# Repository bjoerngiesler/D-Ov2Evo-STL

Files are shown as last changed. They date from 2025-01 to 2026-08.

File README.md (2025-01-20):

# D-Ov2Evo
Bavarian Builders: Felix Beyer, Björn Giesler

## This is an ADD-ON to Michael Baddeley's files!

This GitHub contains modified print files that are to be used as add-ons and partial replacements of Michael Baddeley's D-Ov2. This GitHub does not contain all the files to print a functional droid, you still need parts from [Michael's Patreon](https://www.patreon.com/c/mrbaddeley). We have Michael's express permission to post our modifications on GitHub to better handle file changes, upgrades etc., but will never post all files for a functional droid here.

## What is D-Ov2Evo?

D-Ov2Evo is an extension of Michael Baddeley’s great D-Ov2 design for the D-O Astromech Droid from The Rise of Skywalker. 

D-Ov2 in itself is an extension and improvement of Michael’s original D-Ov1 design. Where D-Ov1 had a central drive axis for the main wheels, D-Ov2 has an excentric Lazy Susan design, which allows fixing the wheels all around the body, giving tremendously higher stability and longevity. Where D-Ov1 had the main neck and head nod servos in the body, D-Ov2 has the head nod servo in the headbox, which greatly improves play in the head assembly.

D-Ov2Evo improves D-O in the following respects.

* All analog servos have been replaced by Dynamixel digital servos, which are serially controlled. This reduces servo play, jitter, and noise. It removes 3 out of 4 servo cables routed through the neck. It also allows much tighter control and diagnostics.
* The motors have been replaced by the same model fitted with quadrature encoders, allowing for individual wheel speed control as part of a more stable control concept. They are also actively cooled so they will never overheat.
* The whole droid is controlled by a central more powerful Arduino, and uses a modern IMU, for tighter control and the opportunity to run free head animation (e.g. turning/leaning the head automatically as the droid drives a curve).
* Power is provided by two easily removable 18650 battery packs, which yield a bit less runtime than the original LiPos but can be changed in seconds without disassembly (and are safer).
* The body takes 5W speakers instead of the original 3W ones, giving much louder sound for conventions.
* A central power supply and distribution board includes a fuse, a voltage monitor, and means much less cabling.
* The head has moving antennas run from their own microcontroller.
* The software is fully open source and published at https://github.com/bjoerngiesler/BBDroids. 

## How to Build!

**Note:** This is not a beginner project. You should have a well working printer, soldering experience, and understanding and alertness to question our instructions. We are not perfect, and there may be bugs.

You will find the print files for D-Ov2Evo in this directory and its subdirectories. The directory structure mirrors the original D-Ov2 directory structure. Each folder underneath here only contains our modified files, not copies of the original print files, so please use the D-Ov2 originals for everything not in here. Each folder also contains an Instructions file, that contains the list of original and modified files for the part, printing and materials advice, and some instructions on assembly.

You will find the systems and wiring diagram, the electronics BOM, and other documentation, in the BBDroids Wiki: https://github.com/bjoerngiesler/BBDroids/wiki/91-Individual-Droid:-D%E2%80%90Ov2Evo If something is not clear, please check the Wiki first, and if you still have questions there is a discussion board at https://github.com/bjoerngiesler/BBDroids/discussions that you can use for questions. Please search before you ask, maybe someone already answered your question!

**Note:** The head with the movable aerials is optional. It is fancy, and we will add more antenna animation as things progress; but it also adds quite some weight to the head and work and cost to your list. You can also simply build the head assembly from the original D-Ov2 plans, with static antennas. Print `HeadStaticAerialsDynamixelCutout.stl` instead of the original head cone, because the roll Dynamixel sticks out at the top and this one has a cutout for it.

## Work in Progress! (But almost done)

D-Ov2Evo has been in development for more than a year. It started with taking a lot of inspiration from Matt Denton’s Dynamixel/Lynxmotion modification of the original D-Ov1.

Over time, we learned, added and modified many things. Björn’s original D-Ov2Evo ran great at a convention for a day, and on the second day one motor burned up… we need active cooling. Getting the batteries out and back in is a huge hassle… we need to modify for removable batteries. The thing is much too silent… we need bigger speakers. You can’t get at the grub screws for the motor gears. The cabling is a mess. And so on and so on. 

We are actively stopping ourselves now from doing any more modifications, it’s time the thing gets tested by other people. But as we publish, we are building two droids as test kits, and making how-to videos. As this slowly progresses, we are going to publish the files to Michael Baddeley’s OneDrive, and we are also going to publish extensive (and hopefully correct :-)) videos that guide through physical build, electronics, control system tuning, and software.

Please bear with us, we’ll arrive at the head eventually.

If you have any questions or suggestions, you can find Felix and Björn in MrBaddeley’s Facebook group, please ping us there in posts or send us PMs.

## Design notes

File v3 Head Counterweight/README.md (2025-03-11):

# Why is a head counterweight significant?

In the original D-O files developed by Michael, the head weight is not balanced by its own counterweight. This means that every head motion changes the body weight distribution, especially if the neck tilts moving the head forward or backward. This causes the body to pitch forward or backward, influencing the body balance controller that is trying its very best to keep the body in equilibrium. Essentially this means that as you bring the head forward, the body pitches forward and starts to drive forward as the controller tries to compensate for that pitch. Not only the neck servo goes into this equation, but also the head motion on the neck itself. This makes the effect hard to compensate by software unless you know the exact weight distribution of all head and neck components and also the speed they are moving at and the torque their motors are enacting on the system.

These effects are the main reason why it is a very good idea to reduce head weight to an absolute minimum, but if we want to have movable aerials in the head for example there are limits to the weight reduction. Adding a counterweight to the head itself helps tremendously to decouple head from body motion, allowing for much more freedom in head materials and actuators.

The counterweight that James designed can add around 1kg of weight to balance out the head weight. Since the head lever is much longer, that additional kg is needed even though the head itself is only about 300g.

# Will the non-counterweight version be supported?

Only with static aerials unfortunately. If you know what you are doing you can certainly get a heavier head to control, all the parameters are there and an article describing how they interact is coming. But it is not easy to remove all residual drift, and remotely supporting this is far beyond the amount of time we can invest. We therefore heavily recommend making this change, even if it needs reprints.

# What do I need to change?

Unfortunately this requires a number of reprints - but it's really worth it!

You need a new main frame and top frame to make room for the counterweight, a new main axle to attach the counterweight to, and of course the counterweight pendulum itself. There is a new servo mount and servo main gear. There is also a new PCB base for the main board (which brings additional advantages and tweaks - e.g. you can now remove the PCB base and main board without unscrewing the top frame). You can find these files here: https://github.com/.../tree/main/v3%20Head%20Counterweight. The pendulum can be printed in one part, there is also a cut version that should be glued together with CA glue.

After printing, fill the main frame with 1-1.5kg of ballast and pour with epoxy. Fill the pendulum up to the brim with ballast, you should be able to get just short of 1kg of weight in there if you use lead. Make sure all the nooks and crannies are filled by shaking and pushing from the top. Epoxy is optional here, because the main bar will hold the ballast in place. If you want you can also fill the main bar with ballast, this is optional as it doesn't contribute a lot. The counterweight does not need to be exact - as you see from the video with just head and counterweight outside the body, the balance is not perfect with mine and it doesn't need to be; we still have the body counterweight and friction in the servo to take care of the delta. But it is a good idea to at least roughly try to assemble head,

Add square nuts to all the holes in main frame, top frame and pendulum, and secure with hot glue.

Set the pendulum aside, assemble servo and servo base, insert into main frame. Make sure the servo gear is at zero before you proceed.

Add the main bar and side panels with the large bearings. Now put the pendulum underneath the main bar into the cutout in the main frame and screw it on.

Add the top frame with power board and the PCB base with main board and cable everything up.

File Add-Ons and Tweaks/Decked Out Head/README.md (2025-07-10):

# Decked Out Head

This directory contains files for what we call the "Decked Out Head". It's a one-piece head with a separate eye tray and eye covers / "lenses" that can be used to add LED "eyes" to D-O. There is also a variant that allows mounting a FPV camera in the head cone.

This head absolutely needs a neck counterweight, it is too heavy otherwise. Even so, it should be printed in LW-PLA for weight reduction. D-O will drive with a decked out head in regular PLA but you will definitely notice the extra weight. At least for the version with the camera mount, it also will not print properly without supports. This definitely makes it a challenging print. Know what you're signing up for :-)

## Parts
* Headlight tint spray (I use https://www.amazon.de/dp/B0CTCSPR32)
* 3 WS2812 LED strips with 20 LEDs each (e.g. https://de.aliexpress.com/item/4000197861280.html)
* Optional FPV camera: Wyvern Link VTX 100mW transmitter (https://de.banggood.com/Emax-Wyvern-Link-AlphaOpenIPC-100mW-Video-Transmitter-VTX-for-RC-Drone-p-2022191.html)
* Optional FPV cam receiver (https://www.banggood.com/Emax-Wyvern-Link-AlphaOpenIPC-100mW-Video-Receiver-VRX-p-2022194.html)
* On the Qt Py in the head, use the board with the Neopixel connector, not the one without. SMD solder the Neopixel connector on first, if it isn't already. Make sure that you also solder the side tabs, as they will take the mechanical strain from inserting the cable later - if you don't there is a good chance of breaking off the connector. Ask me how I know.

## Printing and Assembly Instructions
1. Print the head variant of your choice, and the eye tray. 
2. Print the eye lens three times in regular white PLA.
3. Paint the eye lenses with a couple coats of headlight tint spray until they are as dark as you would like them.
4. Cut 3 LEDs off each of the LED strips, leaving 17 LEDs on each strip. Cut off the side without the cable, and make sure that you leave enough of the soldering pads intact that you can still solder cables to them.
5. Cut the connectors off the end of the cables on 2 of the strips, and strip the ends of the cables with a wire stripper to expose a mm or so of bare wire.
6. Use double sided tape to mount the LED strips in the eye tray. The left eye gets the strip with the connector on it; push the connector through the hole at the top. The strip for the middle eye is mounted upside down; route the cable out the bottom and into the bottom hole on the left strip. The strip for the right eye is mounted with the cable pointing up; route it out the top and into the top hole on the middle strip.
7. Carefully connect the three strips by soldering the cables from the middle to the left and from the right to the middle strip, matching the colors of the cables coming out the other side. Lift the strip ends with the solder pads out of the eye tray for this so you don't heat up the eye tray's PLA.

## Connecting the Neopixel strips
This is a bit awkward for the current generation of boards. We are updating the board but at the moment you have to do some wiring and modification on the connector.

1. SMD solder the connector onto the board if it is not already on - BEFORE soldering the board to the Qt Py. 
2. Solder a wire from the board's +5V input to the pin taking ESP32's +5V input.
3. Solder a wire from the pin taking the ESP32's RX pin (it's the one farthest away from the +5V input on the same side) to the small hole on the board marked "NP" or "Neopixel".
4. Solder the board to the Qt Py using a pin header, connecting all 6 pins on the +5V side of the Qt Py, +5V pin farthest away from the Neopixel connector, USB-C port pointing down.
5. Do not plug the Neopixel strip in yet. Plug the board into USB-C and measure the connection. It should have GND on the pin next to the "NP" hole, the connection to "NP" on the middle pin, and the connection to +5V on the pin closest to the ESP32 board. Make sure that your cable reflects that mapping - black wire is GND, red wire is +5V, and white wire is Data or "NP". You can rewire the cable by carefully lifting up the plastic tabs holding the pins with a needle and gently pulling the pins out and reinserting them into the correct holes.

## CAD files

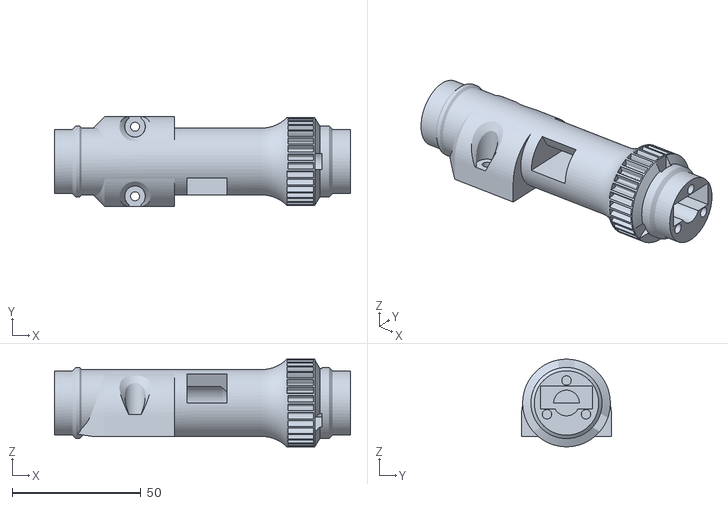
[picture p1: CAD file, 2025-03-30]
MainBar/MainBar_Counterweight_10Pin_Socket_Connector.stl
114.9 x 35.0 x 34.0

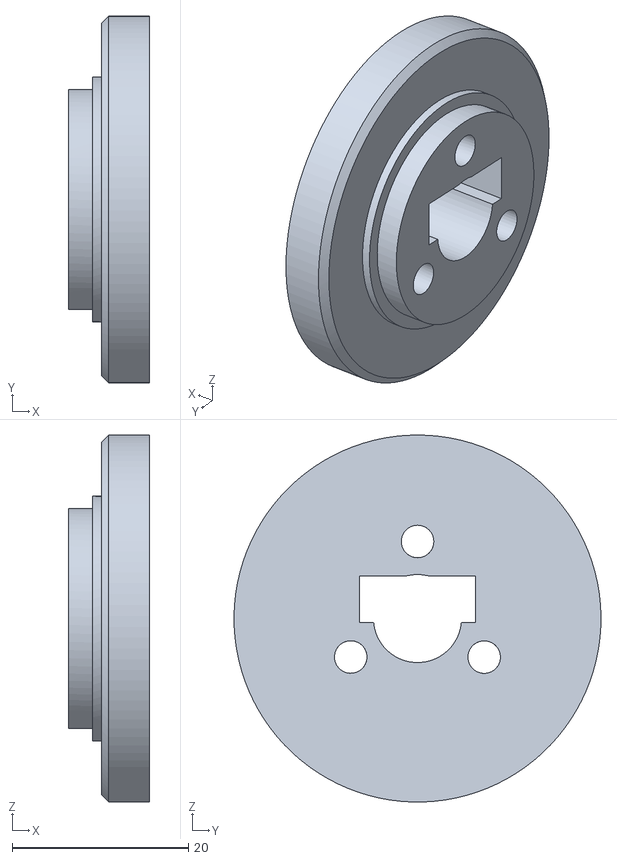
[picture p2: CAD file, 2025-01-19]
MainBar/MainBarHolderB_Connector_Cutout.stl
9.16 x 41.7 x 41.7

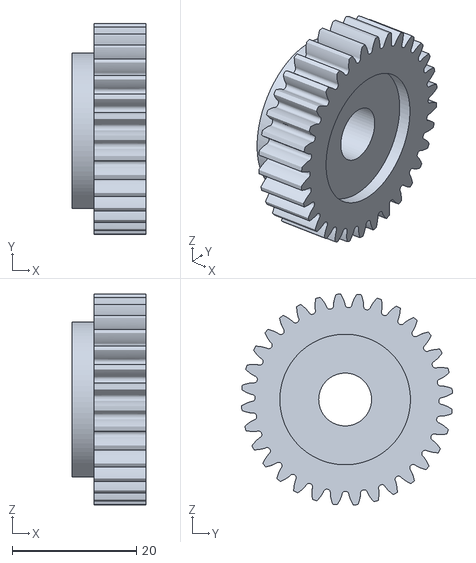
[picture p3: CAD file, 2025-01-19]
MainFrame/Main Servo Gear Dynamixel.stl
11.9 x 33.9 x 33.9

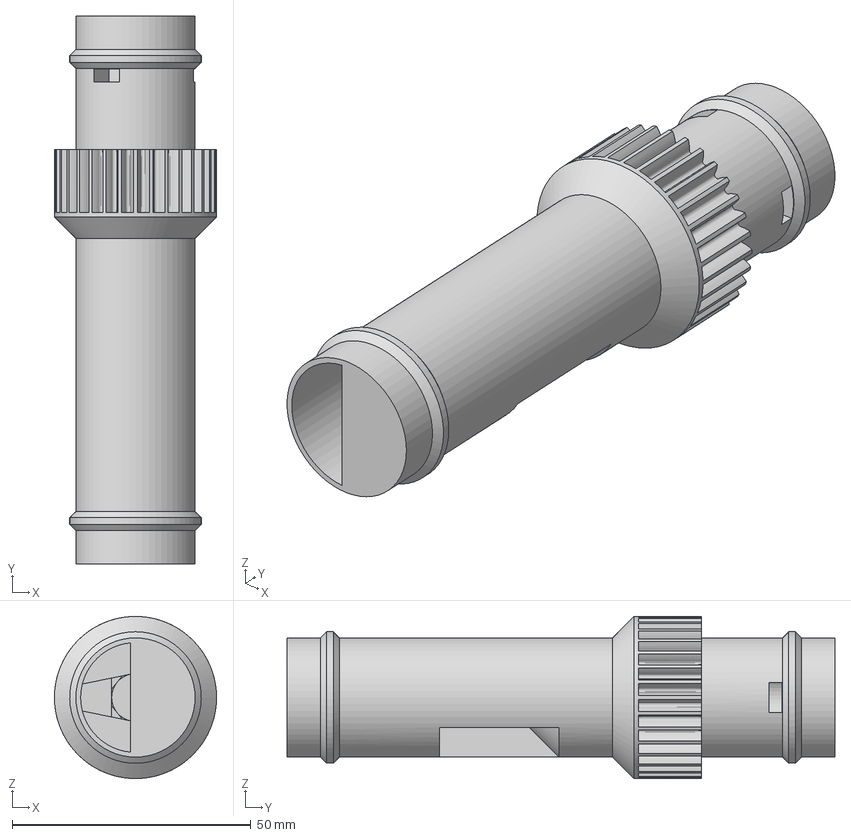
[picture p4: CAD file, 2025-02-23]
MainBar_Counterweight_10Pin_Socket_Connector_Printoptimized.3mf
34.0 x 114.9 x 34.0 mm

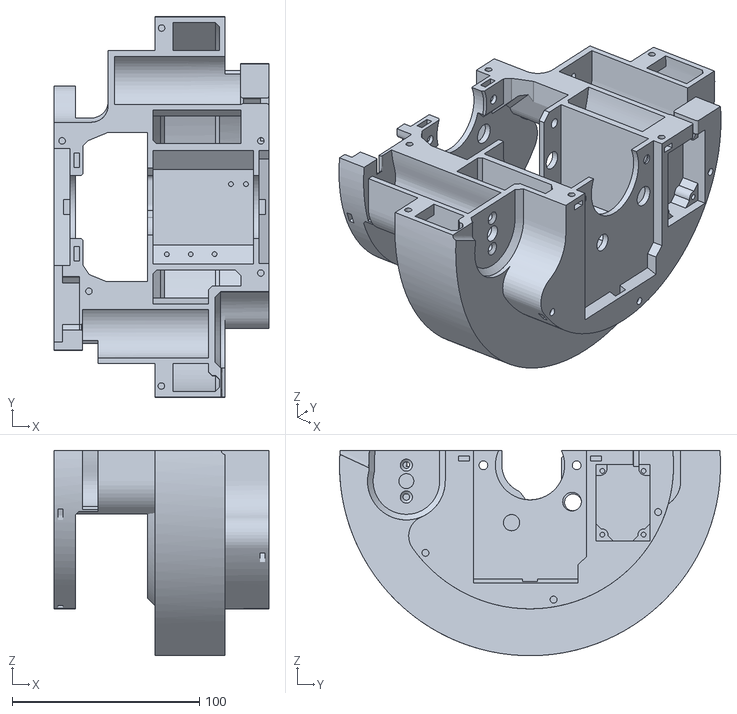
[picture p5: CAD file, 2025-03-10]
v3 Head Counterweight/Mechanics/Main Frame.stl
114.5 x 203.3 x 109.6

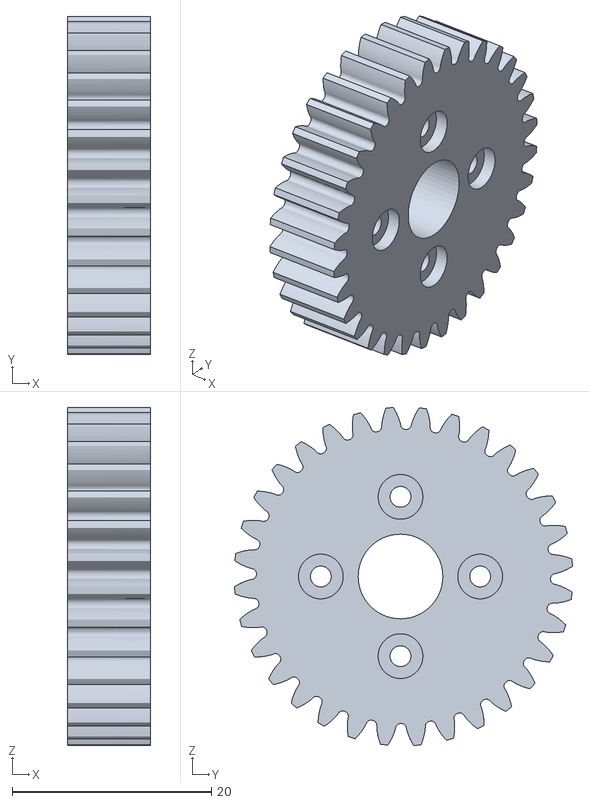
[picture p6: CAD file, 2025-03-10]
v3 Head Counterweight/Mechanics/Main Servo Gear Dynamixel.stl
8.35 x 33.9 x 33.9

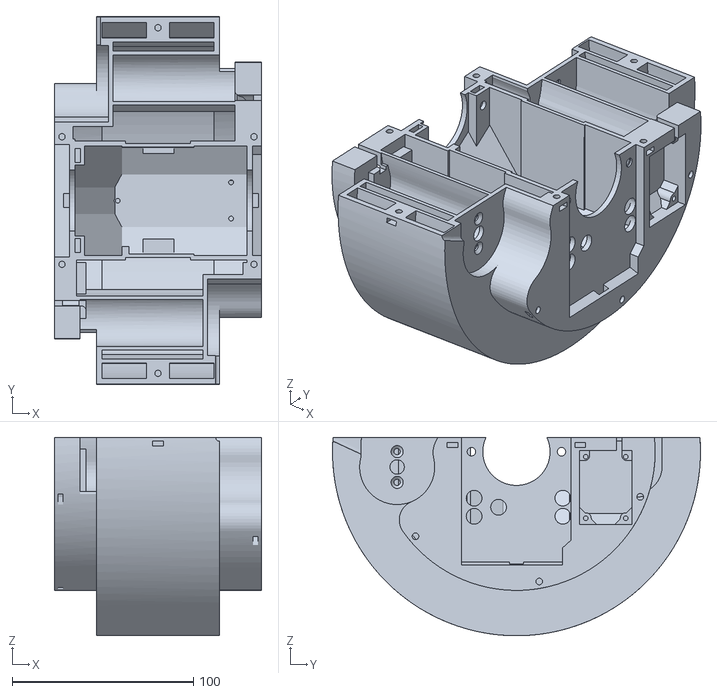
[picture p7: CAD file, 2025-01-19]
MainFrame/Main Frame Dynamixel 5WSpeakers.stl
114.5 x 203.3 x 109.6

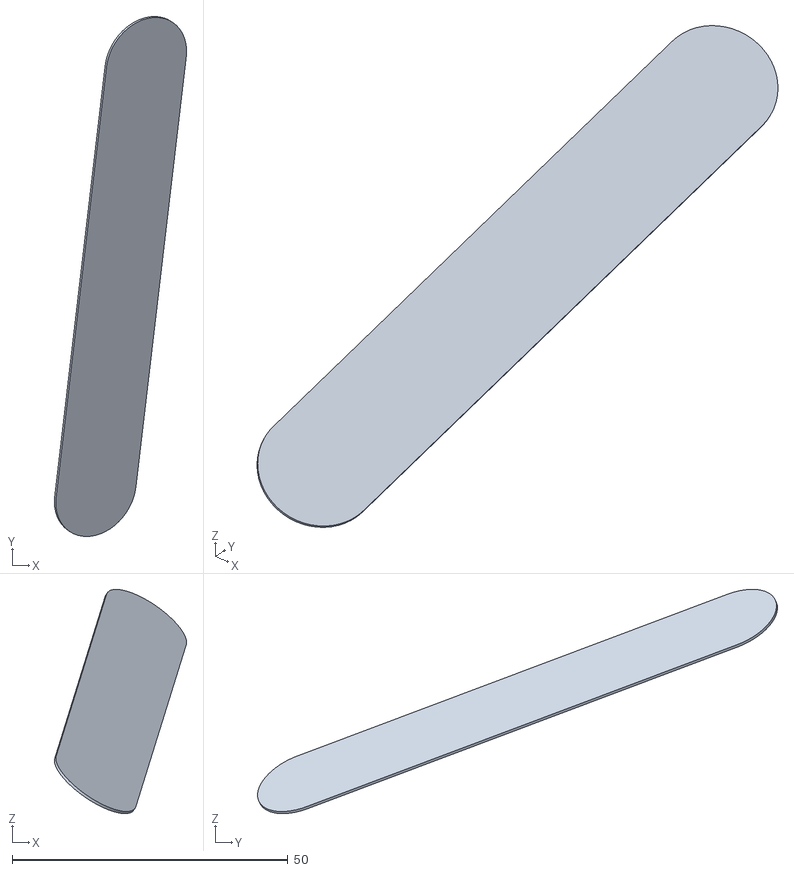
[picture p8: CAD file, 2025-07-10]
Add-Ons and Tweaks/Decked Out Head/Eye Lens x3.stl
24.0 x 94.3 x 40.7

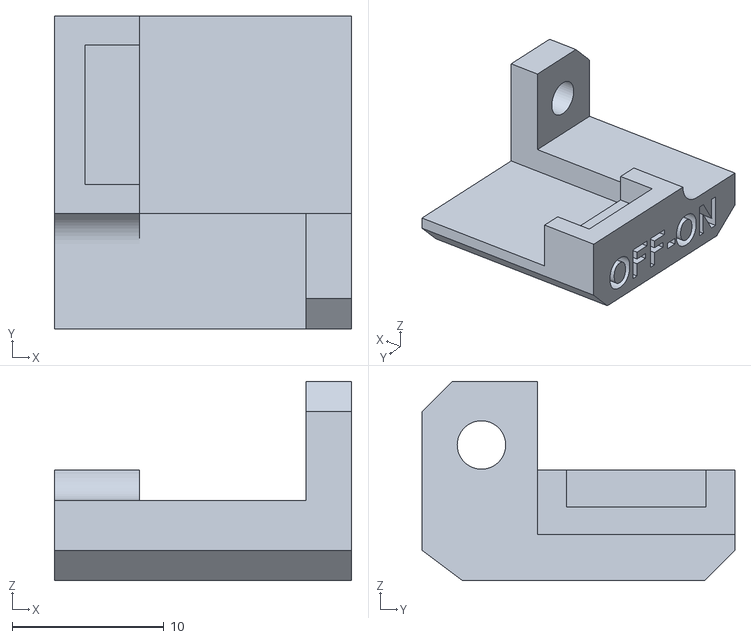
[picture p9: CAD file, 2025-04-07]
Add-Ons and Tweaks/Socket for USB Extension Cable/USB Extension Socket Stop.stl
19.6 x 20.6 x 13.1

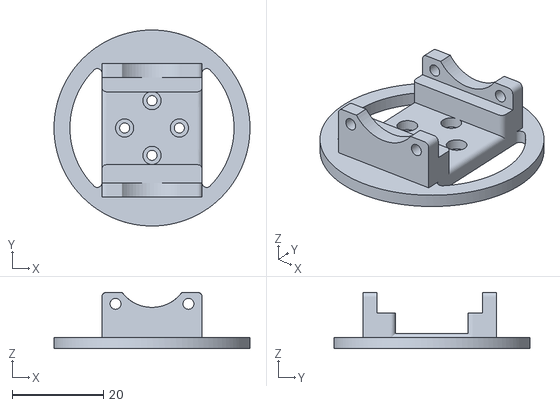
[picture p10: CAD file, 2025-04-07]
Add-Ons and Tweaks/TiltMountDynamixelUnified Stronger.stl
43.0 x 43.0 x 12.4

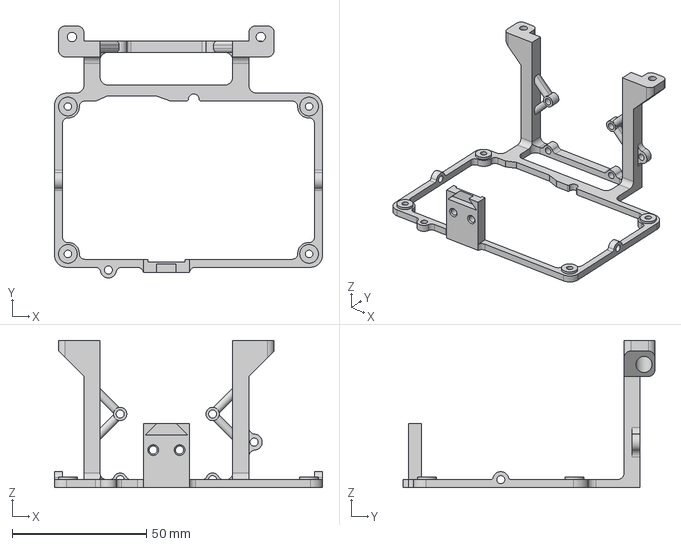
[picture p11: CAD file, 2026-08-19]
Electronic Mount/PCBBase-Modified.step
100.0 x 94.1 x 55.0 mm

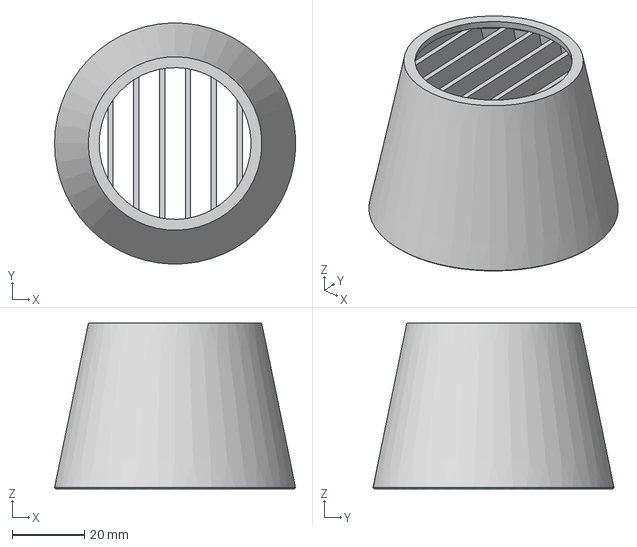
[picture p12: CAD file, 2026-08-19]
Head Moveable Aerials/nose - extra perimeter around grille.step
66.6 x 66.6 x 45.8 mm

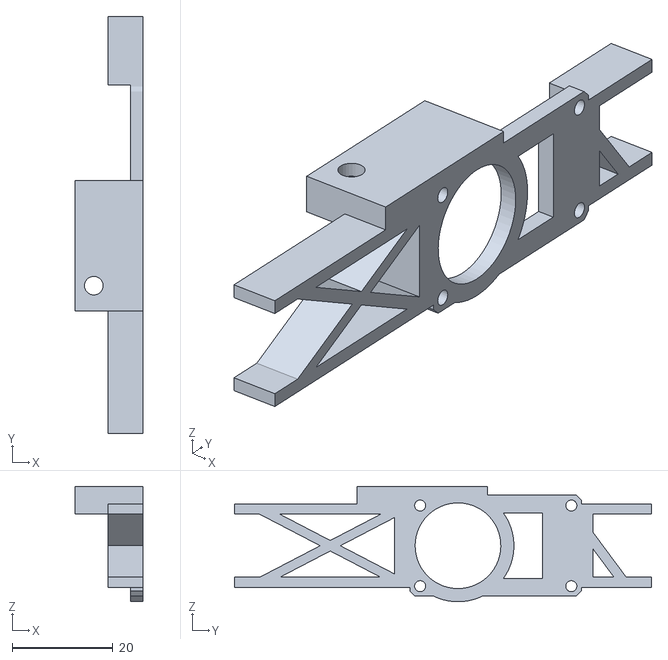
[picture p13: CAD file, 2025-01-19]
HeadBar/HeadFrame Dynamixel.stl
13.5 x 82.7 x 22.9

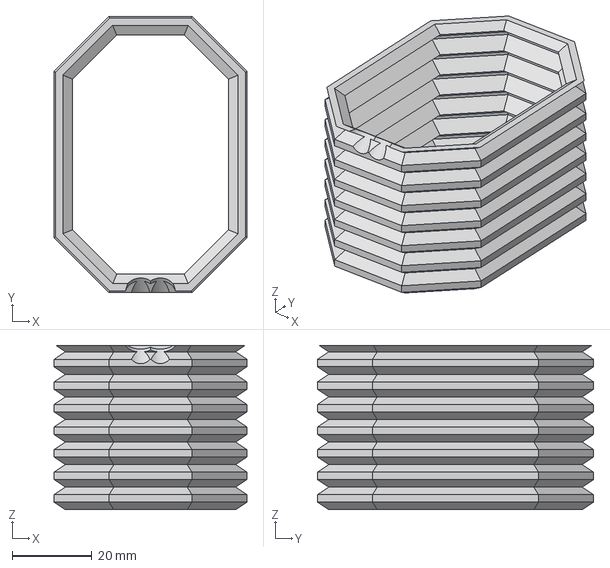
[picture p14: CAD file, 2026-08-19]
HeadBox/Rubber Grommet - Optimized for Vase Mode.step
48.3 x 69.1 x 41.1 mm

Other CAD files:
v3 Head Counterweight/Mechanics/Main Bar Counterweight 10Pin Socket Connector.stl
Lazy Susans/Drive Edge v4.step
MainFrame/Battery Pull Clip.stl
Stand/Stand Bottom D-O Rebel Logo.stl
Add-Ons and Tweaks/Decked Out Head/Eye Tray.stl
Add-Ons and Tweaks/Decked Out Head/Head With Camera Mount.stl
Add-Ons and Tweaks/Decked Out Head/Head Without Camera Mount.stl
Add-Ons and Tweaks/Socket for USB Extension Cable/USB Extension Socket.stl
Electronic Mount/PCBBase-Modified.stl
Electronic Mount/PCBBaseDynamixel.stl
Head Moveable Aerials/AerialArmBracketx3.stl
Head Moveable Aerials/AerialArmx3.stl
Head Moveable Aerials/Head.stl
Head Moveable Aerials/HeadplateDynamixel.stl
Head Moveable Aerials/RearPanel.stl
Head Moveable Aerials/RearPanelPlate.stl
Head Moveable Aerials/ServoFramex3.stl
Head Moveable Aerials/ServoLinkRodx3.stl
Head Moveable Aerials/nose - extra perimeter around grille.stl
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

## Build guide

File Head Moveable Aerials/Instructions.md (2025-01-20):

# D-Ov2Evo Head (Moveable Antennas) Instructions

## Modified Files

Use these modified files:

```
Head.stl
HeadplateDynamixel.stl
RearPanel.stl
RearPanelPlate.stl
ServoFramex3.stl
ServoLinkRodx3.stl
AerialArmx3.stl
AerialArmBracketx3.stl
```

`HeadPlateDynamixel.stl` replaces the one in the `HeadBox` directory.

## Original Files

Use these files from MrBaddeley's original D-Ov2 OneDrive:

```
Nose.stl
AerialBasex3.stl
AerialTipx3.stl
```

**Note** We use a carbon tube (OD 15mm, ID 13mm, 1mm wall thickness) cut to 124mm length instead of the printed Barskin. It's lighter and very slightly more rigid. It's also a good idea to superglue the skin onto the bar after all the cabling has been done, again for extra rigidity.

## Build Notes

This is a bit more involved.

### Caveats

Unfortunately the nano servos are often not OK out of the box. This is frustrating to say the least, and can cause at least two effects (probably more):

* Servos can become stuck in one extreme position, and not budge from there. Since at startup the servo connection pins output zero PWM the servos rush to their zero position, and if they get stuck there we can't move them unless someone moves them manually by turning the little gear. One remedy might be to add a circuit that only powers the servos when the Qt Py can output a sane PWM value. We haven't done that yet, sorry :-/ 
* Some servos just jitter. Some only in specific positions. Since we connect signal and power GND, this is not a GND issue, and we've not found a great way to quieten it.

At the moment the best bet is to swap servos until you've found three that work. They aren't exactly cheap either. Apologies.

### Orientation and Supports

Use your printer's auto-orient feature.

### Tools and hardware

In addition to the printed parts, you need 
* 3 lengths of 1.5mm carbon rod, 150mm each
* another 3 lengths of 1.5mm carbon rod, 12mm each (can also use 1.8mm, or 1.8mmx12mm steel registration pins)
* 3 nano linear servos, this sort: https://www.reichelt.de/de/de/micro-servo-ds15-links-master-ds15l-p258706.html
* an Adafruit Qt Py ESP32S2 microcontroller
* either the Bavarian Builders' D-O head servo adapter, or roll your own with a bit of stripboard (see below)
* some 2.54mm pin headers
* 12 M1.6x3mm or M1.7x3mm screws to hold the servos
* one M3x12mm thumb screw - something that you can tighten with your fingers
* one M3 square nut
* two M3x12mm socket head screws - I use Nylon ones for weight
* 6 M3x6mm socket head screws - I use Nylon ones for weight (and you can shorten them with a knife)
* 6 M1.4x3mm socket head screws
* Short Dynamixel TTL cable

### Material

Use LW-PLA (lightweight, the foaming kind) for `Head.stl`, `HeadPlateDynamixel.stl`, `AerialArmBracketx3.stl`, `Nose.stl` and `AerialTipx3.stl`. Print the head and nose with a single wall, as lightweight as you possibly can. If you want you can also print `AerialBasex3.stl` in LW-PLA, unless you go to conventions, in which case it's probably a better idea to print it in TPU for flexibility should some kid grab your droid by the aerial.

Use TPU for `ServoFramex3.stl`, and print 3 of them. The reason for using TPU is to decouple the servo vibrations. If you can't print TPU you can also print these out of some other material, you'll hear a bit more servo noise, no big deal.

ASA or PLA+ for everything else.

## Assembly

### Rear Panel and Servos

* Tap 8 holes in `RearPanelPlate.stl` for M3: The 6 ones left and right to the rectangular aerial openings, and the two ones on the "legs" that will be used to screw the rear assembly to the head plate.
* Glue `RearPanelPlate.stl` to `RearPanel.stl`, so that the servo holes line up. There are four small holes around the periphery of both parts that you can use for registering the parts together with small screws (1.5mm). 
* Glue the three `ServoFramex3.stl` instances into the recesses in `RearPanelPlate.stl`, each next to an aerial opening.
* Screw the servos into the servo frames, with the nylon drive gear pointing towards the aerial openings. If the screws don't really grip that's no problem, they will hold by friction.
* Put the 12mm rods into the holes of the 3 aerial arms, and put the aerial arms into the holes. The horns are offset from the middle, orient them in such a way that they are on the other side of the corresponding servo's actuator horn.
* Add the aerial arm brackets and screw them down with short M3 socket head screws.
* Connect each servo horn to the corresponding aerial arm using M1.4 screws and the servo link rods.

### Head plate

The servos unfortunately use JST-1.0 connectors and not regular 2.54mm servo connectors like all other servos do. Therefore we need an adapter board or other connectors.

* Make sure that you have flashed the Qt Py with the Arduino sketch in `Arduino/Utilities/AntennaI2CServer`.
* If you use our servo head adapter, solder it to the Qt Py board using pin headers. The pin marked "-" on the servo head adapter connects to "GND" on the ESP32 board, and the first three pins (the ones at the other end of the "-") connect to SCK, MI, MO.
* If you don't use our servo head adapter:
  * Snip off the connectors at the end of the nano servo cables and crimp on regular 3 pin Dupont connectors. Ugly but works. Red cable (VCC) in the middle, black (GND) and white (PWM) on the sides. 
  * Build an adapter with a bit of stripboard. This adapter should have the following connections:
    * A 2-pin header for servo power, GND and +5V. This will come from the topmost Dynamixel.
    * Three 3-pin headers for the servos.
    * Connect GND from the 2-pin header to all 3 servo GNDs, and the Qt Py's GND.
    * Connect +5V from the 2-pin header to all 3 servo VCCs (middle pins), but not to the Qt Py.
    * Connect the servo connectors' PWM pins to SCK, MI, MO on the Qt Py.
  * Solder the adapter to the Qt Py so that Qt Py's GND connects to the adapter GND, and the three PWM pins to SCK, MI, MO.
* If you want to test things out, you can power the servos with an external +5V power supply and connect the Qt Py to your computer, opening a serial terminal to it. The servos should move to the center position. You can enter numbers from 0 to 180 in the serial terminal, and the servos should move to the corresponding position.
* Cut off one side of the Dynamixel TTL cable. Remove the TX cable, leaving only VCC (the middle one) and GND. If you're unsure which one is TX and which one is GND consult the neck wiring picture in https://github.com/bjoerngiesler/BBDroids/wiki/91-Individual-Droid:-D%E2%80%90Ov2Evo This is the power cable we will use for the aerial servos.
* Crimp a 2-pin Dupont connector onto the resulting power cable. Plug the side with the Dynamixel connector into the head roll Dynamixel.

### Aerials

* Glue the aerial tips onto the 1.5mmx150mm carbon rods.
* Glue the carbon roads into the aerial bases.

### Put everything together

* Glue the nose to the head cone.
* Add a M3 square nut into the pocket at the front of the head plate. There's a bit of plastic that covers the screw hole in lieu of support material. Push through this with a small screwdriver and make sure you can screw a thumbscrew into this from the top.
* Screw the servo adapter / Qt Py assembly to the head plate using the single hole in the middle at the back, so that the servo connectors point towards the rear.
* Screw the head plate onto the neck roll servo (front into the servo plate, back into the idler from the FPX330-H101 kit). M1.7 self tapping screws as usual.
* Push the head cone onto the head plate from the front, so that the head plate is underneath the plate inside the head cone.
* Fix the head cone with the thumbscrew at the front.
* Connect the servos to the adapter.
* Connect the Qt Py to the 4-pin i2c cable coming out of the neck, and to the power cable.
* Push the back head assembly into the head cone, first inserting the top latch into its slot at the top of the head, then screwing down head, head plate, and back assembly with two M3 screws from the bottom. For this you have to push the plastic aside on the bottom a bit, using hex socket screws and a hex driver with a rounded head helps.
* Push the aerials into the three aerial arms.

Presto!

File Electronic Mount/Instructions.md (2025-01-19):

# D-Ov2Evo Head (Moveable Antennas) Instructions

## Modified Files

Use these modified files:

```
PCBBaseDynamixel.stl
```

## Original Files

None :-) 

## Build Notes

### Material, Orientation, Printing Tips

Print out of PETG, ABS, ASA, PLA+ or PLA, in order of preference. The slight flexibility of PETG helps here because it allows you to bend the whole thing a bit when the dovetail joint is opened, which can be helpful when routing cables. Prints face down with the legs sticking up.

### Preparation

If you like to tap your plastic for your screws, tap the following:
- 2 holes in the legs
- 4 holes on the side of the legs, where the amplifier mounts
- 4 holes on the top, where the mainboard mounts.

### Assembly

- Use 2 M3 countersunk screws to add the PCB Base to the Top Frame. Length doesn't really matter here, M3x8 or longer will be fine.
- Mount the Top Frame to the Bottom Frame (the one with the lead counterweight) using 6 M3x8 countersunk screws.
- Screw the mainboard onto the PCB Base using 4 M3 socket head screws, can be as short as 4mm or as long as 8mm.
- Screw the amplifier to the side of the PCB Base using 4 M3 socket head screws, can be as short as 4mm or as long as 8mm.

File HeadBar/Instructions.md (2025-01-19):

# D-Ov2Evo HeadBar Instructions

## Modified Files

Use these modified files:

```
HeadFrame Dynamixel.stl
ServoCouple Dynamixel.stl
```

## Original Files

Use these files from MrBaddeley's original D-Ov2 OneDrive:

```
TopBar.stl
Barskin.stl
HeadBar.stl
```

**Note** We use a carbon tube (OD 15mm, ID 13mm, 1mm wall thickness) cut to 124mm length instead of the printed Barskin. It's lighter and very slightly more rigid. It's also a good idea to superglue the skin onto the bar after all the cabling has been done, again for extra rigidity.

## Build Notes

Please check [the Wiki](https://github.com/bjoerngiesler/BBDroids/wiki/91-Individual-Droid:-D%E2%80%90O) for wiring. 

### Orientation and Supports

Use your printer's auto-orient feature.

### Material

ASA or PLA+ for everything. If you don't use a carbon tube but go with the standard printed Barskin, the main bar should definitely not be printed in PETG, it's too flexible and will wobble.

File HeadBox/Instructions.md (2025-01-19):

# D-Ov2Evo HeadBox Instructions

## Print Files

```
HeadBoxA.stl
HeadBoxB.stl
HeadplateDynamixel.stl
NeckBottomDynamixel.stl
NeckTopDynamixel.stl
RubberGrommet.stl
TiltMountDynamixelUnified.stl
```

## Original Files

Use these files from MrBaddeley's original D-Ov2 OneDrive:

```
HeadBoxBar.stl
HeadGreeble.stl
HeadGreebleresin.stl
```

(`HeadGreebleresin.stl` is an optional variant of `HeadGreeble.stl`, don't need both.)

## Build Notes

We use a carbon tube (OD 15mm, ID 13mm, 1mm wall thickness) cut to 124mm length instead of the printed Barskin. It's lighter and very slightly more rigid. Not a big change so if you can't find one just use the original.

It's also a good idea to superglue the skin onto the bar after all the cabling has been done, again for extra rigidity. 

### Connectors

Servo mounts use M1.7x5mm self-tapping screws. You can use M2x5mm if you want but we find 1.7mm holds well. The head roll servo (the topmost one) connects to `HeadplateDynamixel.stl`, it is the only one that needs to be connected in the front and the back of the servo. For the back connection you need an idler, these come in Dynamixel's FPX330-H101 connector set.

### Orientation and supports

These parts are not oriented, your slicer's auto-orient feature will take care of that. No supports needed. **Exception:** `NeckTopDynamixel.stl` has a slightly recessed ring at the top that is not strictly needed but helps with registering the top servos to the bottom assembly. This doesn't come out properly if printed face down, so it's best to print with the two legs on the build plate and adding supports for the arc. 

### Material

Print these out of **LW-PLA** for weight reduction:

```
HeadBoxA.stl
HeadBoxB.stl
NeckBottomDynamixel.stl
```

Print these out of **ABS, ASA, or PLA+** for strength, but regular 2-wall profile works fine, strength profile with many walls would be too heavy:

```
HeadplateDynamixel.stl
HeadBoxBar.stl
NeckTopDynamixel.stl
TiltMountDynamixelUnified.stl
HeadGreeble.stl (or print HeadGreebleresin.stl out of resin)
```

Print this one out of **TPU** (black, paint tends to crack on TPU after a while due to its flexibility). We print this in 1-wall vase mode for weight reduction, which does cause problems with layer adhesion on our printers giving a bit of a "flayed" look. YMMV - try it out!

```
RubberGrommet.stl
```

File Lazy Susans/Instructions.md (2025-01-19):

# D-Ov2Evo Lazy Susans Instructions

This contains only `Drive Edge For Flex Tire Countersunk.stl`, an optional part that replaces the original `DriveEdge.stl` in the `Optional Flex Drivetyres` directory. It is only slightly modified to allow for more room for the countersunk screws that hold the small bearings in. I found these stood out a bit too far and sometimes rubbed against the body.

Apart from this one, the original Lazy Susans are unmodified. We heavily recommend the flex tyre variant!

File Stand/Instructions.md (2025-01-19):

# D-Ov2Evo Stand Instructions

Quick and rough swivel stand. Uses the same ball bearing as D-O's center axle.

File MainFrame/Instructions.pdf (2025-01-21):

# D-Ov2Evo - Main Frame

# Parts List, Printing Tips

### Last change: Aug 24, 2024

# Parts List

### Use these parts from the original MrBaddeley folder MainFrame:

- Frontframeinsert.stl
Print 1, any material, no supports

### Use these parts from the D-Ov2Evo folder Body:

- Battery Mount Clamp 18650 x4.stl

### Print 4, any material, on side, no supports

- Battery Mount L 18650.stl
Print 1, any material, no supports
- Battery Mount R 18650.stl
Print 1, any material, no supports
- Main Frame Dynamixel 5WSpeakers.stl Print 1, PETG, ABS or ASA, supports recommended
- Main Servo Gear Dynamixel.stl
Print 1, any material, no supports
- Rear Frame Insert.stl
Print 1, any material, no supports
- Servo Base Dynamixel 0.0.stl to Servo Base Dynamixel -1.0.stl
You need one of these but probably need to print several or all, see below. Any material, no supports.
- Top Frame Dynamixel 18650.stl
Print 1, any material, supports recommended

# Hardware and Bought Parts List

# Fasteners

### - M3 square nuts (x16) - M3x8mm countersunk bolt (x17) - M3x6mm round head bolt (x12) - M2x6mm self-tapping bolt (x6) - M4x8mm countersunk bolt (x2) - M4x12mm countersunk bolt (x2) - M4 square nuts (x4)

# Motors

### - Pololu-4863 encoder motors (medium power, 12VDC, 20.4:1 gearbox) (x2) - Dynamixel XL430-W250-T servo (x1)

# Other Hardware

### - Lead shot or steel bearings for ballast. 1-3mm diameter. Finer grain or dust is not recommended. How much you use is going to vary (heavier robots are more stable but drive

slower and put more load on the bearings), but you will not need more than 3kg.

### - 4mm Flange Motor Coupler H12D10 (x2) - Bearing 6805-2RS (x2) - 5mmx5mm rare metal magnets - cylinder (x4)

# Other Bought Parts

### - Keystone 1049 battery holder for dual 18650 batteries (x2) - XT30 female plugs (x2) - XT30 mount PCB (x2) — e.g. AliExpress, see pic: - 18650 LiPo batteries (x4) — use the largest capacity (mAh) you can find - 8 Ohm 5W speakers, this kind: These have an outside size

of 70mm x 31mm x 16mm.

### - Nano fans (20x20x6mm) 12V, e.g. AliExpress (x2) - 2 component epoxy resin or epoxy glue - AWG22 wire

# Tools

### - Screw drivers - Soldering iron and solder - Wire cutters and strippers - Hot glue gun - Super glue - Loctite

# Printing Tips

# Material

We always recommend using ASA if you can print it (printer has an enclosure), but most of these

### can be printed in any material really, with one notable exception: Main Frame: If you intend to use poured resin to fix the counterweight in the body, as we

recommend, PLA+ is not a good idea at least for Main Frame Dynamixel 5WSpeakers.stl, because the resin gets hot when curing. So if you print everything else in PLA+, make sure this one is PETG at least.

# Strength

All the load bearing parts (Main Frame Dynamixel 5WSpeakers.stl, Main Servo Gear Dynamixel.stl, Top Frame Dynamixel 18650.stl) should be printed in your printer’s strength profile, or if it doesn’t have one, with the following settings:
- Layer height: .2mm
- Perimeters: 6 or more
- Bottom layers: 6 or more

- Top layers: 6 or more
The inserts (Frontframeinsert.stl, Rear Frame Insert.stl) are visible and should be printed in the finest resolution your printer can offer, or even in resin.
All other parts can be printed any way you please.

## Orientation and Supports

Contrary to Mr Baddeley’s practice, these parts are not oriented the way they should be printed, but your printer’s auto-orient feature will take care of that for most items.
Notable exception: Battery Mount Clamp 18650 x4.stl should be printed on the side, to

### strengthen it in the direction it will take the highest load, like so:

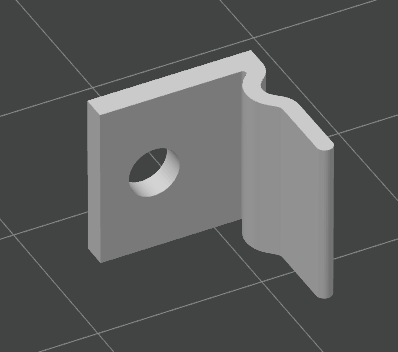
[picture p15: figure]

### No supports are needed for most parts, with the following notable exceptions: Main Frame Dynamixel 5WSpeakers.stl should get manual supports, painted on the

surfaces marked in green in the pictures here (and the surfaces marked in turquoise are those the

### print stands on:

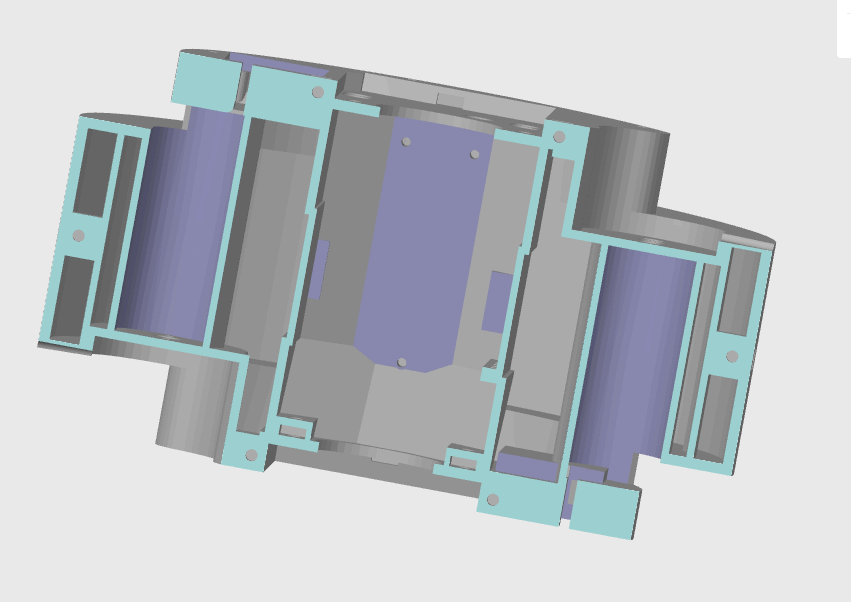
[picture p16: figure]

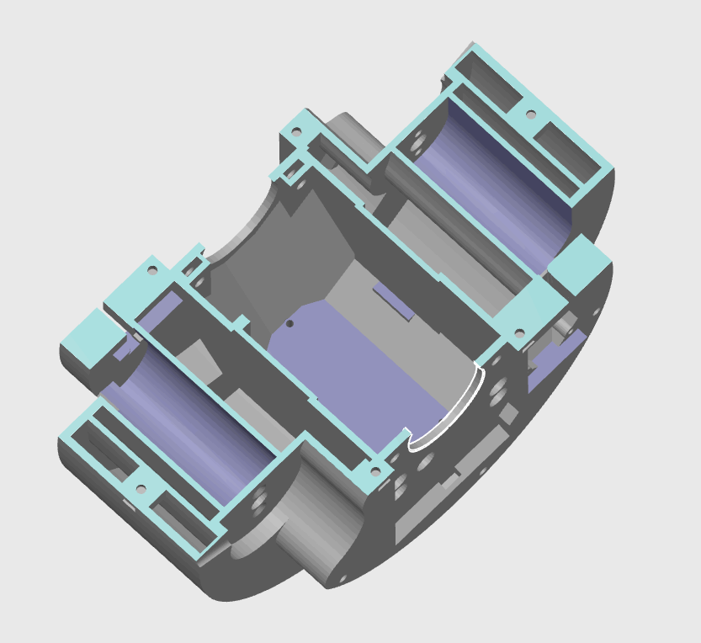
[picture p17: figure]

Top Frame Dynamixel 18650.stl should get automatic supports.

## Assembly

Please refer to the tutorial video for assembly instructions. In short and for reference:

## Main Frame

1. Fill the main frame with about 1kg of ballast. Fix the ballast by pouring some epoxy resin on top, or if you don’t have experience with resin you can also use epoxy glue. In this case we recommend self-mixing dual barrel epoxy syringes. Let cure.
2. When the resin has cured, insert 12 square M3 nuts into the recesses around the body (3 on each side, 6 on top) and fix with hot glue.

3. Insert 2 square M4 nuts into the recesses at the top of the droid (left side, where the frame insert goes) and fix with hot glue.
4. Break open the loudspeakers with a flathead screwdriver and lever out the inner plastic frame with the actual speaker. Clear the holes of the plastic frame, these are glued in and often something stays stuck.
5. Insert the loudspeakers into the openings on both sides of the main frame and fasten with 4x round head screws each.
6. Insert the two Pololu motors into the motor wells. This is a tight fit; if needed, remove the rear plastic cap over the encoder. Fix with 2x M3 countersunk bolts each.

## Servo

1. Screw the main servo gear onto the servo front using the screws that come with the servo.
2. Insert the servo into one of the Servo Bases. Use the one without a number for now. Fasten it with 3 of the screws that come with the servo.
3. Insert the servo base with the servo into the main frame and fasten it with 3 M3 countersunk bolts. These should self tap. Be careful not to overtighten.
4. Later when you add the main bar, you may need to replace the servo base by a different one; these lower the servo deeper into the body in .2mm steps. You want a tight fit for the main bar but you don’t want to put too much pressure onto the servo gear. If you feel pressure use a base with a bigger number.

## Frame Inserts

1. Insert two M4 square nuts into the rear frame insert and (verrrrry carefully) fix with hot glue, don’t overspill!
2. Push the large bearings into both inserts.
3. Screw the rear frame insert into the frame with M4x8mm bolts.

## Battery Boxes

1. Solder the XT30 female connectors onto the holder PCBs.
2. Bridge the -/+ pins on one end of each battery holder by soldering a wire across.
3. Solder two wires to the -/+ pins on the other side of the battery holder.
4. Thread the wires through the passage on the printed battery mounts.
5. Solder the wires to an XT30 connector/PCB assembly each, so that the battery pack’s + connects to the square end of the XT30 connector and the - connects to the chamfered end.
6. Fix the battery holders to the printed battery mounts using round head screws.
7. Fix the connector PCBs to the printed battery mounts using M2 self-tapping screws.

## Top Frame

1. Add the 4 battery mount clamps to the top frame by fastening them with M3 countersunk screws (from the bottom) and adding a square nut on the top. They should orient so that their flat part points towards the front and back of the droid, while their 90° raised part points towards each other. If you want you can fix the screws in place by adding a drop of Loctite to the nuts on top.
2. Add the fans by fixing them with self-tapping bolts from the underside. The fan output should point into the round air vents.

3. Screw the top frame to the bottom frame using 6 M3 countersunk bolts.
4. Superglue 4 5x5 round neodymium magnets into the recesses on the left and right.

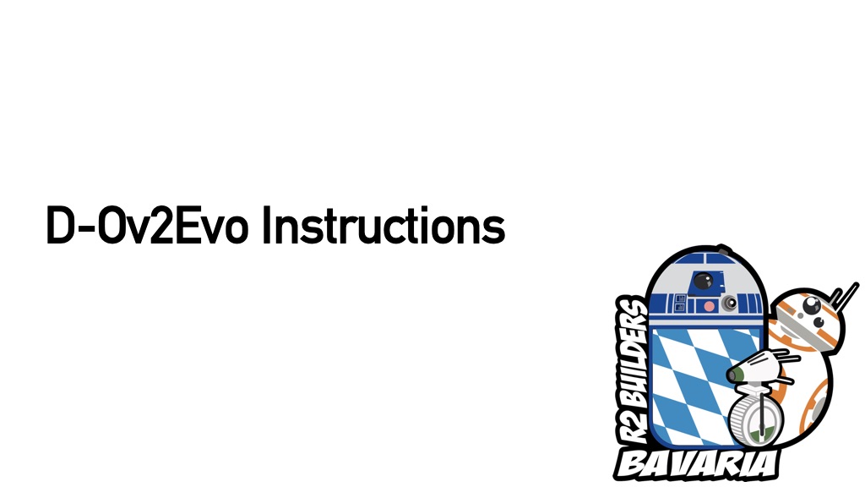
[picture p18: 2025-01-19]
Instructions.key/preview.jpg

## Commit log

2025-01-19 Inserted layers into main servo gear for support-free printing
    [Main Servo Gear Dynamixel.stl]
2025-01-20 Fixed oversight in "Head Movable Antennas/Instructions.md"
2025-01-23 Updated Head Verions
    Added the Cut out and some ease of print Features
    [Undented Head 65degree cutout.stl, Undented Head.stl]
2025-01-29 Modified the Main Bar for ease of Print
    Added some Bridging Geometry.
    [MainBar_Counterweight_10Pin_Socket_Connector_Printoptimized.3mf, MainBar_Counterweight_10Pin_Socket_Connector_Printoptimized.stl]
2025-02-23 Registering holes added
    [RearPanel.stl]
2025-03-10 Head Counterweight added
    [Dynamixel Cable Guard Top Deck.stl, Lighter Head Rear panel Aerial.stl, Main Bar Counterweight 10Pin Socket Connector.stl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]
2025-03-11 README and battery pull clip added
    [Battery Pull Clip.stl]
2025-03-20 Rename Main Frame Instructions.pdf to Instructions.pdf
2025-03-30 James fixed the gear shoulder so it doesn't collide with the servo housing anymore
    [MainBar_Counterweight_10Pin_Socket_Connector.stl]
2025-04-07 Add-ons and tweaks directory added
    [TiltMountDynamixelUnified Stronger.stl, USB Extension Socket Stop.stl, USB Extension Socket.stl]
2025-05-04 Gear shortened for better fit
    [Main Bar Counterweight 10Pin Socket Connector.stl]
2025-07-10 Decked out head added
    [Eye Lens x3.stl, Eye Tray.stl, Head With Camera Mount.stl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]
